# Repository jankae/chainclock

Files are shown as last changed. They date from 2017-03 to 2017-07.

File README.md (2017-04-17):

# chainclock

The chainclock is a very inaccurate clock which displays the time by means of rotating a chain.

<p align="left">
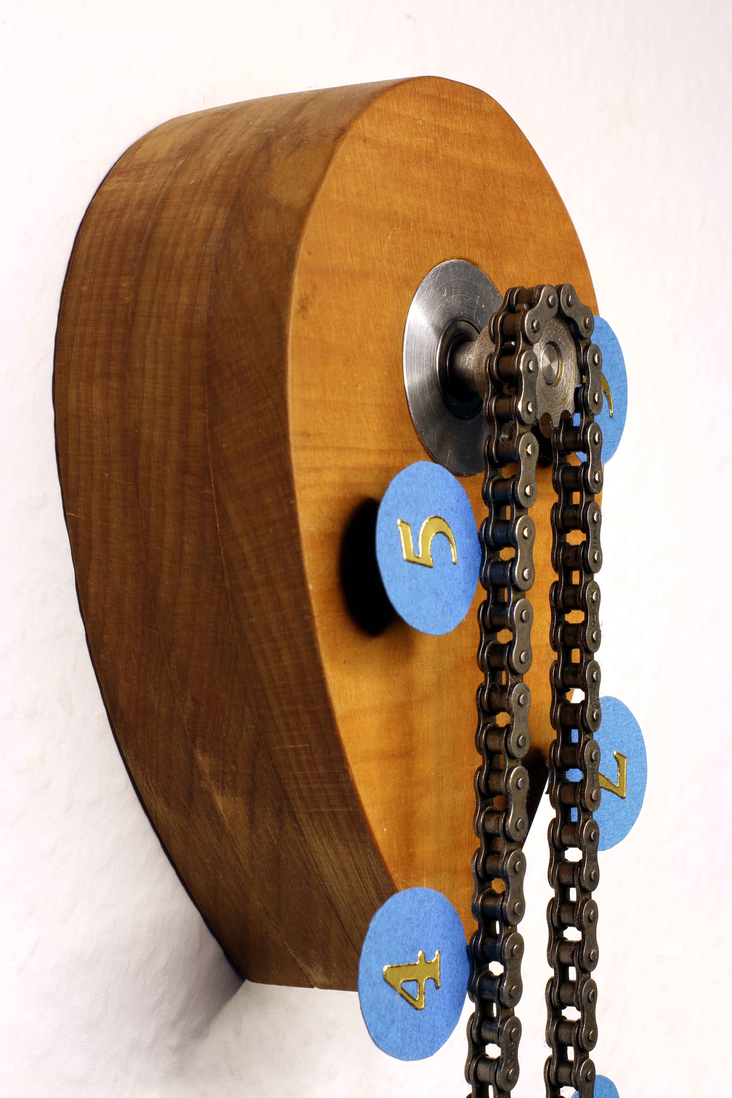
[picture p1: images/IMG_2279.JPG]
  
</p>

The chain-loop consists of 120 links, with a number attached to every 10th link. Since the driving gear has ten teeth, this results in one rotation per hour. After some failed experiments with attaching the gear to the hour hand of a normal clock (it was either too loud, too weak or both), I opted for a 28BYJ-48 stepper motor.

This also called for a microcontroller (ATtiny2313) with the simpliest of programs. To save energy, the motor doesn't continually move. Instead it is only activated whenever a minute has passed. The microcontroller performs a few steps, checks the voltage and goes back to sleep.

The clock is powered by a 3,7V Lipo battery and stops completely if the battery runs low (there is no further indicator, the clock simply stops until the battery is replaced).

## Construction
The central part is the stepper motor (28BYJ-48). Some additional aluminium, a ball bearing to lighten the load on the motor (should be fine even without it) and a teardrop wooden enclosure completes the clock.

## Compiling & Flashing
1. See PCB-files for the pinout of the ISP connector. 
2. Adjust the makefile to your programmer
3. Setting fuses:

  ```
  cd software
  make fuses
  ```
4. Flash the program:

  ```
  make flash
  ```
  ## Operation
  Attach the chain and sit back ;)

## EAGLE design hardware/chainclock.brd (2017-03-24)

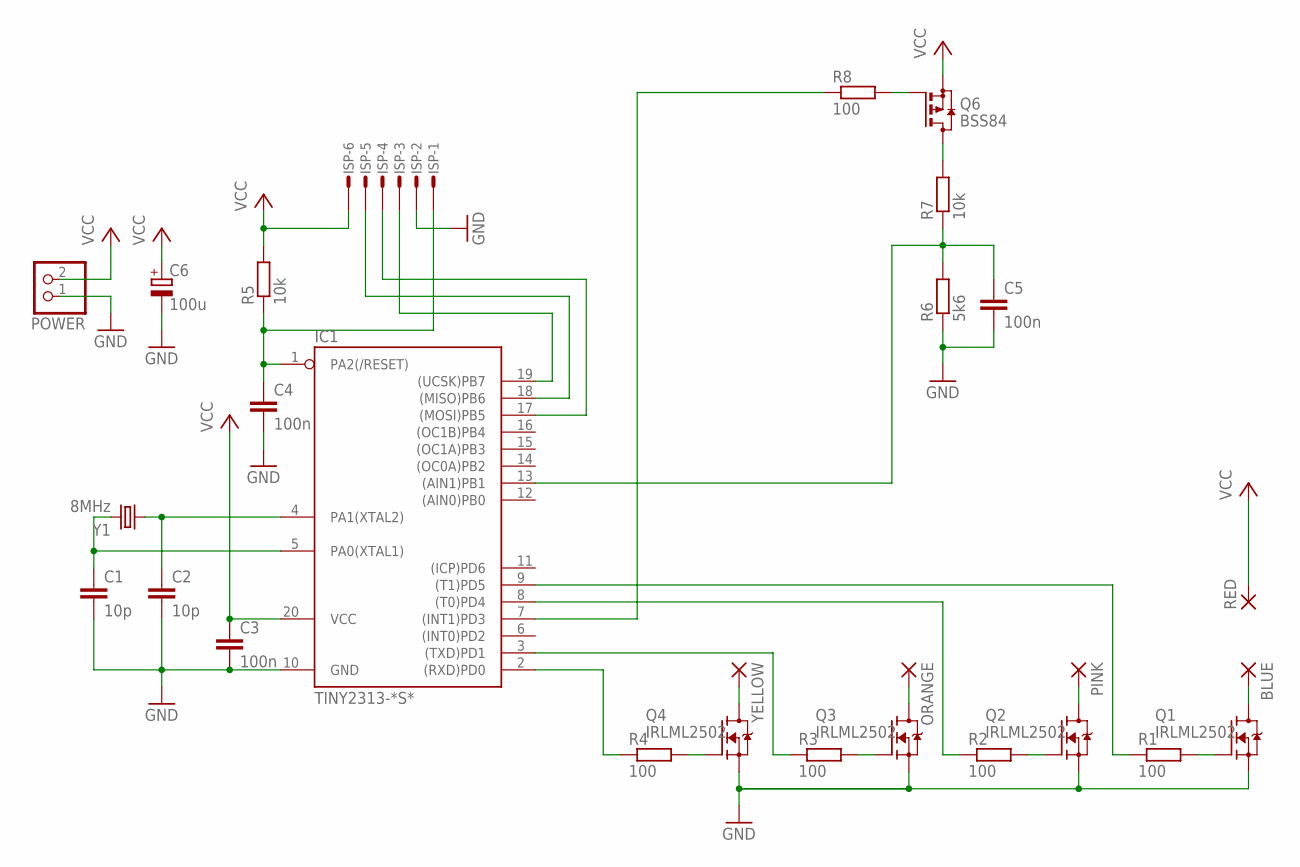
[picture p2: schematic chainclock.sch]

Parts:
BLUE: SMD2; SMD1,27-2,54
C1, C2: 10p; C0603
C3, C4, C5: 100n; C0603
C6: 100u; E2,5-6
IC1: TINY2313-*S*; SO20L$
ISP: MICROMATCH-6SMF; MMT-F-SMD-6
ORANGE: SMD2; SMD1,27-2,54
PINK: SMD2; SMD1,27-2,54
POWER: PINHD-1X2/90; 1X02/90
Q1, Q2, Q3, Q4: IRLML2502; SOT23-3
Q6: BSS84; SOT23
R1, R2, R3, R4, R8: 100; R0603
R5, R7: 10k; R0603
R6: 5k6; R0603
RED: SMD2; SMD1,27-2,54
Y1: 8MHz; HC49UP
YELLOW: SMD2; SMD1,27-2,54

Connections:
GND: C1.2, C2.2, C3.2, C4.2, C5.2, C6.-, IC1.10 (GND), ISP.2, POWER.1, Q1.2 (S), Q2.2 (S), Q3.2 (S), Q4.2 (S), R6.1
unnamed: Q3.1 (G), R3.2
unnamed: Q4.1 (G), R4.2
unnamed: Q2.1 (G), R2.2
unnamed: Q1.1 (G), R1.2
unnamed: C4.1, IC1.1 (PA2(/RESET)), ISP.1, R5.1
unnamed: Q4.3 (D), YELLOW.1
unnamed: ORANGE.1, Q3.3 (D)
unnamed: PINK.1, Q2.3 (D)
unnamed: BLUE.1, Q1.3 (D)
unnamed: C2.1, IC1.4 (PA1(XTAL2)), Y1.1
unnamed: C1.1, IC1.5 (PA0(XTAL1)), Y1.2
unnamed: IC1.19 ((UCSK)PB7), ISP.3
unnamed: C5.1, IC1.13 ((AIN1)PB1), R6.2, R7.1
unnamed: IC1.9 ((T1)PD5), R1.1
unnamed: IC1.8 ((T0)PD4), R2.1
unnamed: IC1.2 ((RXD)PD0), R4.1
unnamed: Q6.3 (D), R7.2
unnamed: Q6.1 (G), R8.2
unnamed: IC1.7 ((INT1)PD3), R8.1
unnamed: IC1.3 ((TXD)PD1), R3.1
unnamed: IC1.17 ((MOSI)PB5), ISP.4
unnamed: IC1.18 ((MISO)PB6), ISP.5
VCC: C3.1, C6.+, IC1.20 (VCC), ISP.6, POWER.2, Q6.2 (S), R5.2, RED.1

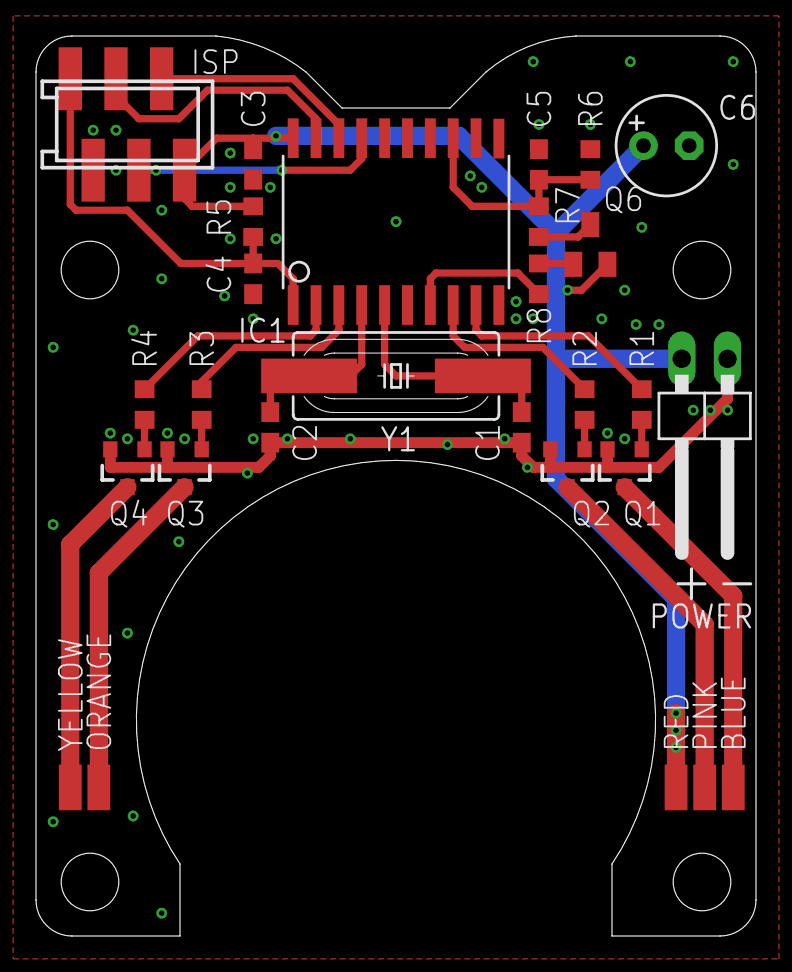
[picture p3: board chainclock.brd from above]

Board: 2 copper layers, 40.0 x 50.0 mm, 28 parts (0 on the bottom side), 24 nets.

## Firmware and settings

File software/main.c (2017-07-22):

#include <avr/io.h>
#include <avr/interrupt.h>
#include <avr/sleep.h>
#include <util/delay.h>

#define BLUE_HIGH()		(PORTD |= (1<<PD5))
#define BLUE_LOW()		(PORTD &= ~(1<<PD5))

#define PINK_HIGH()		(PORTD |= (1<<PD4))
#define PINK_LOW()		(PORTD &= ~(1<<PD4))

#define ORANGE_HIGH()		(PORTD |= (1<<PD1))
#define ORANGE_LOW()		(PORTD &= ~(1<<PD1))

#define YELLOW_HIGH()		(PORTD |= (1<<PD0))
#define YELLOW_LOW()		(PORTD &= ~(1<<PD0))

/* counter for the motor steps */
/* 1019/15 steps per minute needed */
/* needed rotations*15 -> 1019 of this per minute */
uint16_t neededRotations15;

uint8_t minuteParts;
uint8_t minuteFlag;

uint8_t stepCnt = 0;

uint8_t batteryLow = 0;

void waitms(uint16_t ms) {
	for (; ms > 0; ms--)
		_delay_ms(1);
}

void stopMotor(void) {
	ORANGE_LOW();
	YELLOW_LOW();
	PINK_LOW();
	BLUE_LOW();
}

void moveStep(void) {
	stepCnt += 1;
	if (stepCnt >= 8)
		stepCnt = 0;
	switch (stepCnt) {
	case 0:
		ORANGE_HIGH();
		YELLOW_LOW();
		PINK_LOW();
		BLUE_LOW();
		break;
	case 1:
		ORANGE_HIGH();
		YELLOW_HIGH();
		PINK_LOW();
		BLUE_LOW();
		break;
	case 2:
		ORANGE_LOW();
		YELLOW_HIGH();
		PINK_LOW();
		BLUE_LOW();
		break;
	case 3:
		ORANGE_LOW();
		YELLOW_HIGH();
		PINK_HIGH();
		BLUE_LOW();
		break;
	case 4:
		ORANGE_LOW();
		YELLOW_LOW();
		PINK_HIGH();
		BLUE_LOW();
		break;
	case 5:
		ORANGE_LOW();
		YELLOW_LOW();
		PINK_HIGH();
		BLUE_HIGH();
		break;
	case 6:
		ORANGE_LOW();
		YELLOW_LOW();
		PINK_LOW();
		BLUE_HIGH();
		break;
	case 7:
		ORANGE_HIGH();
		YELLOW_LOW();
		PINK_LOW();
		BLUE_HIGH();
		break;
	}
}

void moveOneMinute(void) {
	neededRotations15 += 1019;
	minuteParts = 0;
	minuteFlag = 0;
	uint8_t additionalRotations = neededRotations15 / 15;
	neededRotations15 -= additionalRotations * 15;
	/* enable analog comparator for detecting low battery */
	ACSR &= ~(1 << ACD);
	/* select bandgap reference */
	ACSR |= (1 << ACBG);
	/* enable voltage divider */
	PORTD &= ~(1 << PD3);
	while (additionalRotations > 0) {
		moveStep();
		waitms(3);
		additionalRotations--;
	}
	if (ACSR & (1 << ACO)) {
		/* bandgap (1.1V) is higher than battery voltage after voltage divider */
		/* -> battery low */
		batteryLow = 1;
	}
	stopMotor();
	/* disable ADC and voltage divider */
	PORTD |= (1 << PD3);
	ACSR |= (1 << ACD);
	ACSR &= ~(1 << ACBG);
}

int main(void) {
	neededRotations15 = 0;
	/* disable analog comparator to save energy */
	ACSR |= (1 << ACD);
	/* Set motor pins at output */
	DDRD |= 0b00110011;
	/* Set voltage divider enable pin as output */	
	DDRD |= 0b00001000;
	/* enable all pullups on unused pins */
	PORTD = 0b11000100;
	PORTB = 0b11111101;
	/* disable voltage divider */
	PORTD |= (1 << PD3);
	/* disable digital input buffer on PB1 (AIN1) */
	DIDR |= (1 << AIN1D);
	/* configure timer 1 to use as wake-up call each minute */
	/* prescaler = 64, CTC mode */
	OCR1A = 62499; /* -> 15 compare matches per minute */
	TCCR1B |= (1 << CS11) | (1 << CS10) | (1 << WGM12);
	TIMSK |= (1 << OCIE1A);
	/* configure sleep mode */
	set_sleep_mode(SLEEP_MODE_IDLE);
	sei();
	while (1) {
		sleep_mode()
		;
		if (minuteFlag)
			moveOneMinute();
		if (batteryLow) {
			/* battery voltage is too low */
			/* -> disable all periphery and enter deep sleep mode */
			stopMotor();
			TCCR1B = 0;
			cli();
			set_sleep_mode(SLEEP_MODE_PWR_DOWN);
			sleep_mode()
			;
			/* should never reach this point */
			for (;;)
				;
		}
	}
}
ISR(TIMER1_COMPA_vect) {
	minuteParts++;
	if (minuteParts >= 15) {
		minuteFlag = 1;
		minuteParts -= 15;
	}
}

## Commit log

2017-03-24 voltage divider resistor values fixed
    [chainclock.brd, chainclock.sch]
2017-04-17 Gerber files
2017-04-17 Motor delay reduced
2017-07-22 Motor step time increased

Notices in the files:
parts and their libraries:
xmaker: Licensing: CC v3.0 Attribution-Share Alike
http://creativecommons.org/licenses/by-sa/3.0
